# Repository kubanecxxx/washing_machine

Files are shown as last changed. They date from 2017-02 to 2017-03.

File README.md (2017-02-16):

# washing_machine
Old automatic washing machine electronic controller

This is and old washing machine renovation. The main reason for this project is the old mechanical programmer got cracked and the price for a new one was almost price of a new washing machine.

The project page is hosted on hackaday.io: https://hackaday.io/project/19873-washing-machine-renovation

Machine itself
----
Washing machine type is <b>Ardo A900</b>. It has basic features like:
- two speed motor with 5uF condenser
- water filling valve
- water drain pump
- water heater
- front door electric lock
- low and high level water level switch
- temperature switch
- few front panel switches (most of them are not used any more)

Hardware part
-----

Schematics and board layout are drawed in Eagle version 6. I used STM32F100C6 micronctroller.

The reason for using triacs instead of relays was switching in zero crossing of sine voltage. I used relays in previous version of this project and I had a lot of problems with this. Relay contacts got welded, switching caused microcontroller unhandled exceptions etc.

With triacs there are no more problems with MCU unhandled exceptions. But the water heater triac dissipates almost 10Watts of heat. It means <b>huge heatsink</b> is needed.

Software part
----

Software is based on ChibiOS real time operating system for microntollers. I made [CMake fork](https://github.com/kubanecxxx/chibios_fork) of the ChibiOS - it is my repositories. You probably need to clone this repository to build this project or you can take the data from the [CMakeLists.txt](fw/CMakeLists.txt) and create a ChibiOS Makefile or just edit the CMakeLists (you will probably need to adjust path to the GCC toolchain and path to the ChibiOS directory) to build this project on you machine.

Development toolchain is GNU arm gcc (https://launchpadlibrarian.net/209776202/gcc-arm-none-eabi-4_9-2015q2-20150609-linux.tar.bz2) version 4.9 - it contains interesting newlib library which saves a lot of RAM and hardware floating point support and many other features.

You can flash the MCU via openocd or my [kstlink](https://github.com/kubanecxxx/kstlink) project which is simple gdb server to debug and flash STM microcontrollers (I feel openocd too heavy).

Firmware is not well documented yet.

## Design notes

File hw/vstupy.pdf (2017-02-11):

List1

Stránka 1

vstupy
PA3 | door locked
PA4 | fuse zbytek ok
PA5 | fuse motor ok
PA6 | fuse heat ok
PB13 | low level | hladinoměr nízká úroven
PB14 | high level | hladinoměr vysoká úroven
PB15 | temperature termostat
PA8 | nezdimat | přepínač předvolba neždímat

výstupy
PA7 | lock | zamčít
PB0 | valve | napouštět
PB1 | pump | vypouštět
PB2 | M3 | motor rychle
PB10 | M2 | motor pomalu jeden směr
PB11 | M1 | motor pomalu druhý směr
PB12 | heat | topit

ovládání
PA0 | TIM2_CH1 | enkoder A
PA1 | TIM2_CH2 | enkoder B
PA2 | | enkoder switch
PB8 | I2C1_SCL | I2C display přemapovat I2C1
PB9 | I2C1_SDA | I2C display přemapovat I2C1

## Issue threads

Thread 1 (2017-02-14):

hardware update HW1.2

kubanecxxx, 2017-02-14:
Schematic and board should be updated.
----

- Heating triac is out of board right now -  there should be a connector for it
- there are a lot of neutral wires - dedicated connector with 3 or 4 wires just for neutral
- backup battery is much bigger than thought - holes for the battery holder (cable tie) should be elsewhere

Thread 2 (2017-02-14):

State machine status rememeber after powerdown

kubanecxxx, 2017-02-14:
Current state - automatic state machine is reset during powerup.

+ State machine should be memorised
+ After powerup the GUI should ask for continue or restart

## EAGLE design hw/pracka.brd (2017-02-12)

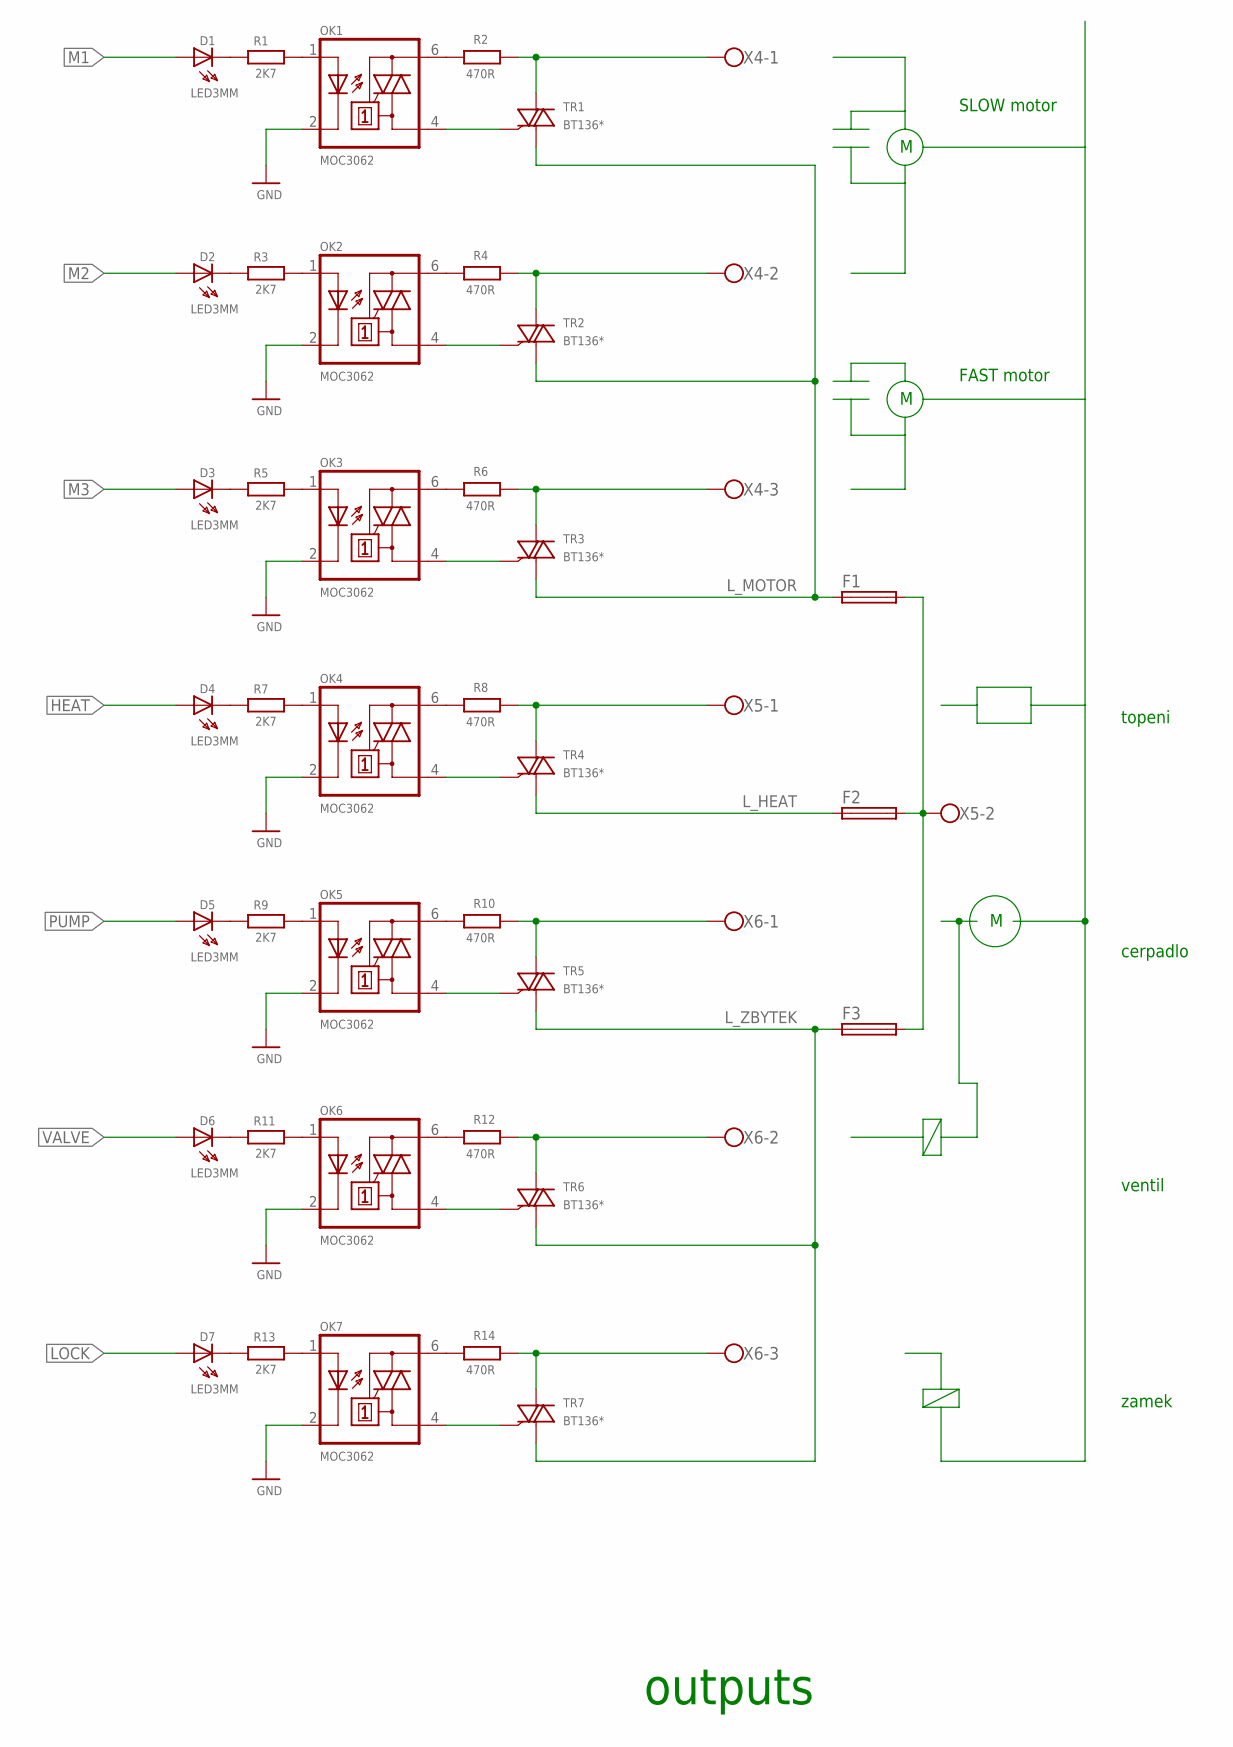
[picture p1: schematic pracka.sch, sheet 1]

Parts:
D1, D2, D3, D4, D5, D6, D7: LED3MM; LED3MM@1
F1, F2, F3: SH22,5A
OK1, OK2, OK3, OK4, OK5, OK6, OK7: MOC3062; DIL06
R1, R3, R5, R7, R9, R11, R13: 2K7; R0805
R2, R4, R6, R8, R10, R12, R14: 470R; 0207/7
TR1, TR2, TR3, TR4, TR5, TR6, TR7: BT136*; TO220DS
X4: W237-03P; W237-133
X5: W237-02P; W237-132
X6: W237-3E

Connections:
GND: OK1.2 (K), OK2.2 (K), OK3.2 (K), OK4.2 (K), OK5.2 (K), OK6.2 (K), OK7.2 (K); also elsewhere on the board
HEAT: D4.A; also elsewhere on the board
LOCK: D7.A; also elsewhere on the board
L_HEAT: F2.1, TR4.A1; also elsewhere on the board
L_MOTOR: F1.1, TR1.A1, TR2.A1, TR3.A1; also elsewhere on the board
L_ZBYTEK: F3.1, TR5.A1, TR6.A1, TR7.A1; also elsewhere on the board
M1: D1.A; also elsewhere on the board
M2: D2.A; also elsewhere on the board
M3: D3.A; also elsewhere on the board
unnamed: OK1.1 (A), R1.2
unnamed: OK2.1 (A), R3.2
unnamed: OK2.4 (A1), TR2.G
unnamed: D1.K (C), R1.1
unnamed: D2.K (C), R3.1
unnamed: OK1.4 (A1), TR1.G
unnamed: OK2.6 (A2), R4.1
unnamed: OK3.1 (A), R5.2
unnamed: OK3.4 (A1), TR3.G
unnamed: D3.K (C), R5.1
unnamed: OK3.6 (A2), R6.1
unnamed: OK4.1 (A), R7.2
unnamed: OK4.4 (A1), TR4.G
unnamed: D4.K (C), R7.1
unnamed: OK4.6 (A2), R8.1
unnamed: OK5.1 (A), R9.2
unnamed: OK5.4 (A1), TR5.G
unnamed: D5.K (C), R9.1
unnamed: OK5.6 (A2), R10.1
unnamed: OK6.1 (A), R11.2
unnamed: OK6.4 (A1), TR6.G
unnamed: D6.K (C), R11.1
unnamed: OK6.6 (A2), R12.1
unnamed: OK7.1 (A), R13.2
unnamed: OK7.4 (A1), TR7.G
unnamed: D7.K (C), R13.1
unnamed: OK7.6 (A2), R14.1
unnamed: F1.2, F2.2, F3.2, X5.2
unnamed: OK1.6 (A2), R2.1
PUMP: D5.A; also elsewhere on the board
P_HEAT: R8.2, TR4.A2, X5.1
P_LOCK: R14.2, TR7.A2, X6.3
P_M1: R2.2, TR1.A2, X4.1
P_M2: R4.2, TR2.A2, X4.2
P_M3: R6.2, TR3.A2, X4.3
P_PUMP: R10.2, TR5.A2, X6.1
P_VALVE: R12.2, TR6.A2, X6.2
VALVE: D6.A; also elsewhere on the board

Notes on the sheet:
topeni
cerpadlo
ventil
zamek
outputs
SLOW motor
FAST motor

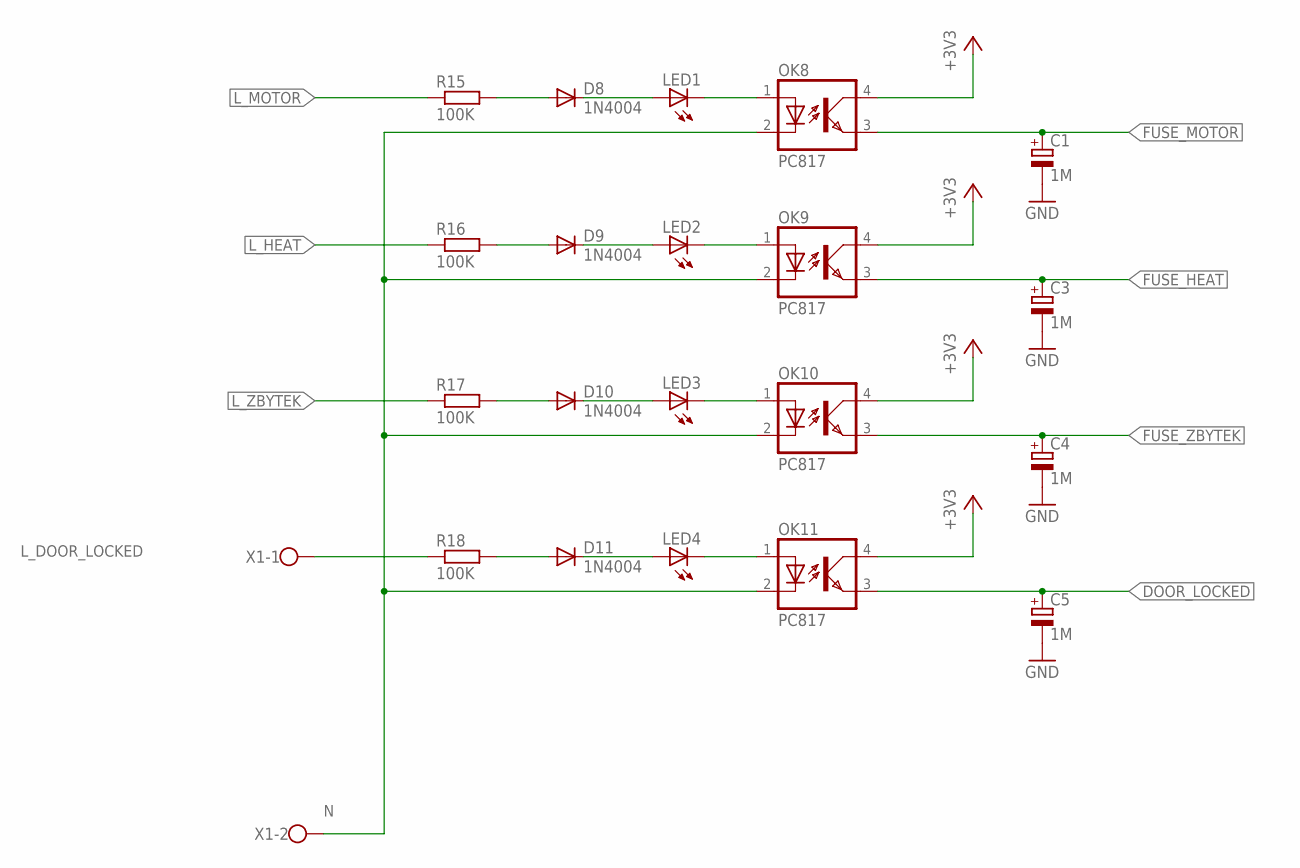
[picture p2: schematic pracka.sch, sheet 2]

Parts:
C1, C3, C4, C5: 1M; E2,5-5
D8, D9, D10, D11: 1N4004; DO41-10
LED1, LED2, LED3, LED4: LED3MM
OK8, OK9, OK10, OK11: PC817; DIL04
R15, R16, R17, R18: 100K; 0207/7
X1: W237-02P; W237-132

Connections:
+3V3: OK8.4 (COL), OK9.4 (COL), OK10.4 (COL), OK11.4 (COL); also elsewhere on the board
DOOR_LOCKED: C5.+, OK11.3 (EMIT); also elsewhere on the board
FUSE_HEAT: C3.+, OK9.3 (EMIT); also elsewhere on the board
FUSE_MOTOR: C1.+, OK8.3 (EMIT); also elsewhere on the board
FUSE_ZBYTEK: C4.+, OK10.3 (EMIT); also elsewhere on the board
GND: C1.-, C3.-, C4.-, C5.-; also elsewhere on the board
L_DOOR_LOCKED: R18.1, X1.1
L_HEAT: R16.1; also elsewhere on the board
L_MOTOR: R15.1; also elsewhere on the board
L_ZBYTEK: R17.1; also elsewhere on the board
N: OK8.2 (C), OK9.2 (C), OK10.2 (C), OK11.2 (C), X1.2
unnamed: D8.A, R15.2
unnamed: D8.C, LED1.A
unnamed: LED1.K (C), OK8.1 (A)
unnamed: D9.A, R16.2
unnamed: D9.C, LED2.A
unnamed: LED2.K (C), OK9.1 (A)
unnamed: D10.A, R17.2
unnamed: D10.C, LED3.A
unnamed: LED3.K (C), OK10.1 (A)
unnamed: D11.A, R18.2
unnamed: D11.C, LED4.A
unnamed: LED4.K (C), OK11.1 (A)

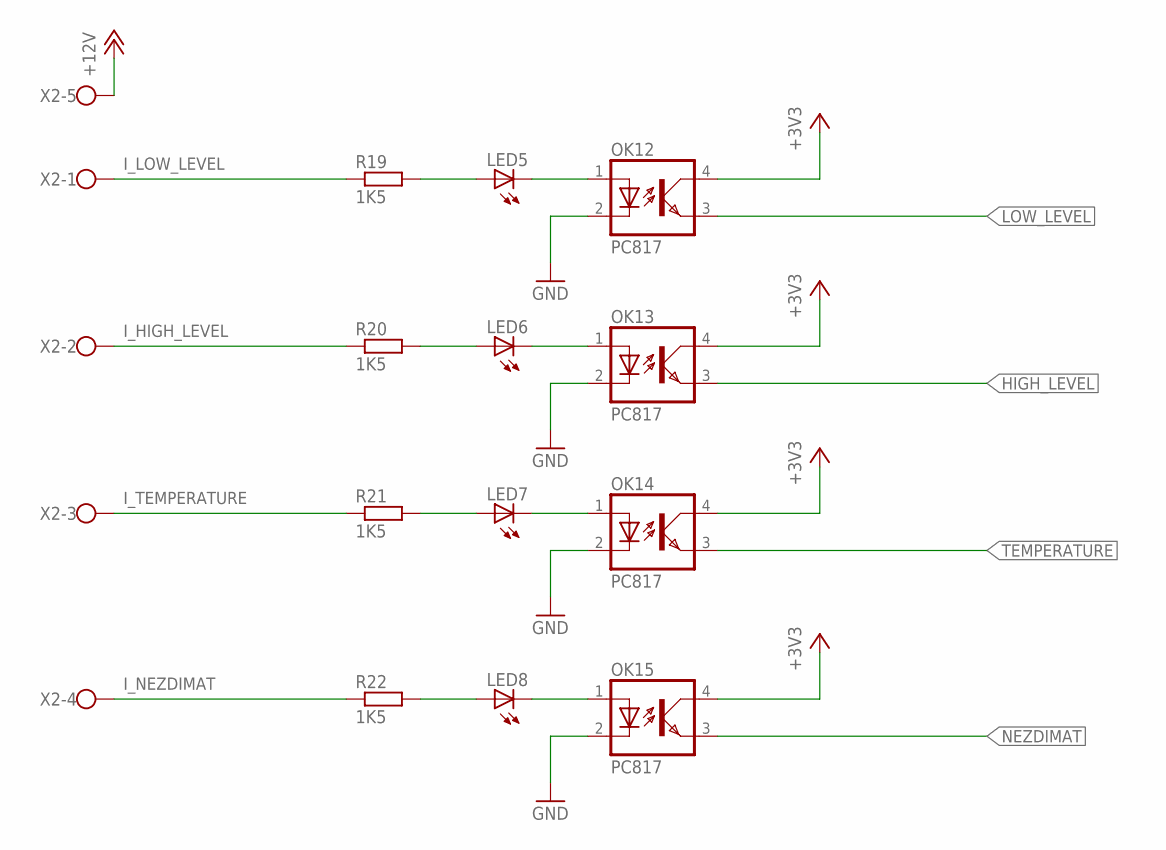
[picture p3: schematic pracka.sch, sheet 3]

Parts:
LED5, LED6, LED7, LED8: LED3MM
OK12, OK13, OK14, OK15: PC817; DIL04
R19, R20, R21, R22: 1K5; R0805
X2: W237-05P; W237-5P

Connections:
+3V3: OK12.4 (COL), OK13.4 (COL), OK14.4 (COL), OK15.4 (COL); also elsewhere on the board
+12V: X2.5; also elsewhere on the board
GND: OK12.2 (C), OK13.2 (C), OK14.2 (C), OK15.2 (C); also elsewhere on the board
HIGH_LEVEL: OK13.3 (EMIT); also elsewhere on the board
I_HIGH_LEVEL: R20.1, X2.2
I_LOW_LEVEL: R19.1, X2.1
I_NEZDIMAT: R22.1, X2.4
I_TEMPERATURE: R21.1, X2.3
LOW_LEVEL: OK12.3 (EMIT); also elsewhere on the board
unnamed: LED5.A, R19.2
unnamed: LED6.K (C), OK13.1 (A)
unnamed: LED5.K (C), OK12.1 (A)
unnamed: LED6.A, R20.2
unnamed: LED7.K (C), OK14.1 (A)
unnamed: LED7.A, R21.2
unnamed: LED8.K (C), OK15.1 (A)
unnamed: LED8.A, R22.2
NEZDIMAT: OK15.3 (EMIT); also elsewhere on the board
TEMPERATURE: OK14.3 (EMIT); also elsewhere on the board

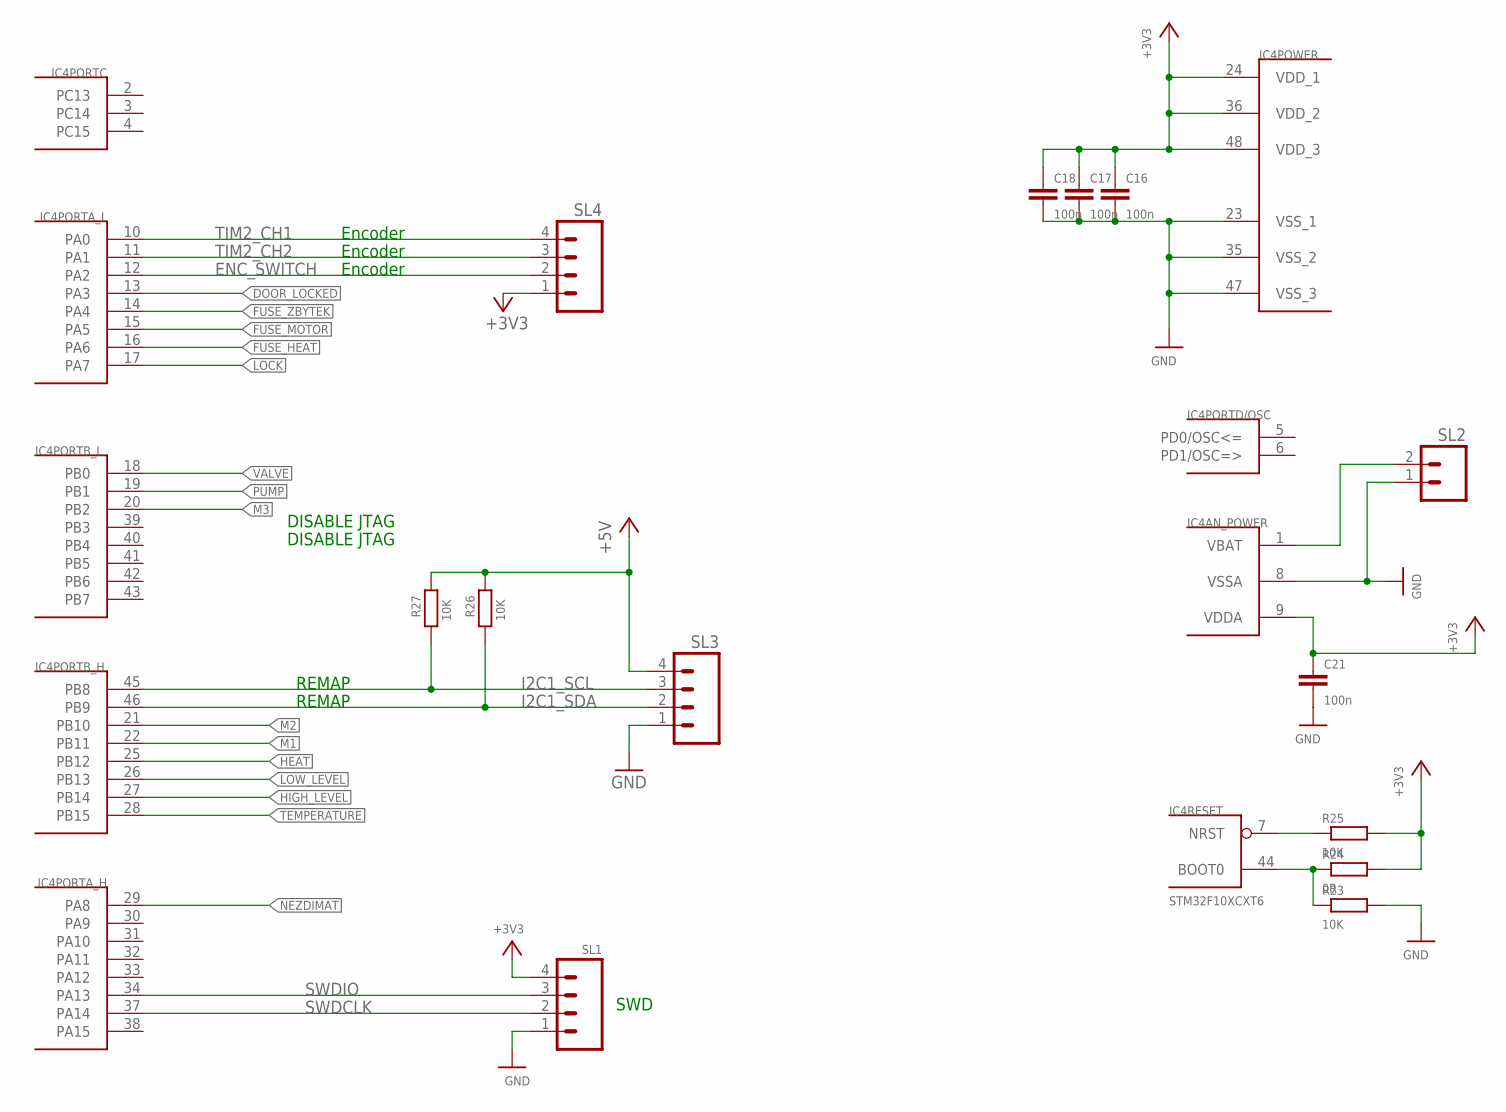
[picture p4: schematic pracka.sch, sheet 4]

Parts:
C16, C17, C18, C21: 100n; C1206
IC4: STM32F10XCXT6; TQFP48
R23, R25, R26, R27: 10K; R0805
R24: 0R; R0805
SL1, SL3, SL4: M04; 04P
SL2: M02; 02P

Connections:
+3V3: C16.1, C17.1, C18.1, C21.1, IC4.9 (VDDA), IC4.24 (VDD_1), IC4.36 (VDD_2), IC4.48 (VDD_3), R24.2, R25.2, SL1.4, SL4.1; also elsewhere on the board
+5V: R26.2, R27.2, SL3.4; also elsewhere on the board
DOOR_LOCKED: IC4.13 (PA3); also elsewhere on the board
ENC_SWITCH: IC4.12 (PA2), SL4.2
FUSE_HEAT: IC4.16 (PA6); also elsewhere on the board
FUSE_MOTOR: IC4.15 (PA5); also elsewhere on the board
FUSE_ZBYTEK: IC4.14 (PA4); also elsewhere on the board
GND: C16.2, C17.2, C18.2, C21.2, IC4.8 (VSSA), IC4.23 (VSS_1), IC4.35 (VSS_2), IC4.47 (VSS_3), R23.2, SL1.1, SL2.1, SL3.1; also elsewhere on the board
HEAT: IC4.25 (PB12); also elsewhere on the board
HIGH_LEVEL: IC4.27 (PB14); also elsewhere on the board
I2C1_SCL: IC4.45 (PB8), R27.1, SL3.3
I2C1_SDA: IC4.46 (PB9), R26.1, SL3.2
LOCK: IC4.17 (PA7); also elsewhere on the board
LOW_LEVEL: IC4.26 (PB13); also elsewhere on the board
M1: IC4.22 (PB11); also elsewhere on the board
M2: IC4.21 (PB10); also elsewhere on the board
M3: IC4.20 (PB2); also elsewhere on the board
unnamed: IC4.44 (BOOT0), R23.1, R24.1
unnamed: IC4.1 (VBAT), SL2.2
NEZDIMAT: IC4.29 (PA8); also elsewhere on the board
NRST: IC4.7 (NRST), R25.1
PUMP: IC4.19 (PB1); also elsewhere on the board
SWDCLK: IC4.37 (PA14), SL1.2
SWDIO: IC4.34 (PA13), SL1.3
TEMPERATURE: IC4.28 (PB15); also elsewhere on the board
TIM2_CH1: IC4.10 (PA0), SL4.4
TIM2_CH2: IC4.11 (PA1), SL4.3
VALVE: IC4.18 (PB0); also elsewhere on the board

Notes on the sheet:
SWD
REMAP
Encoder
DISABLE JTAG

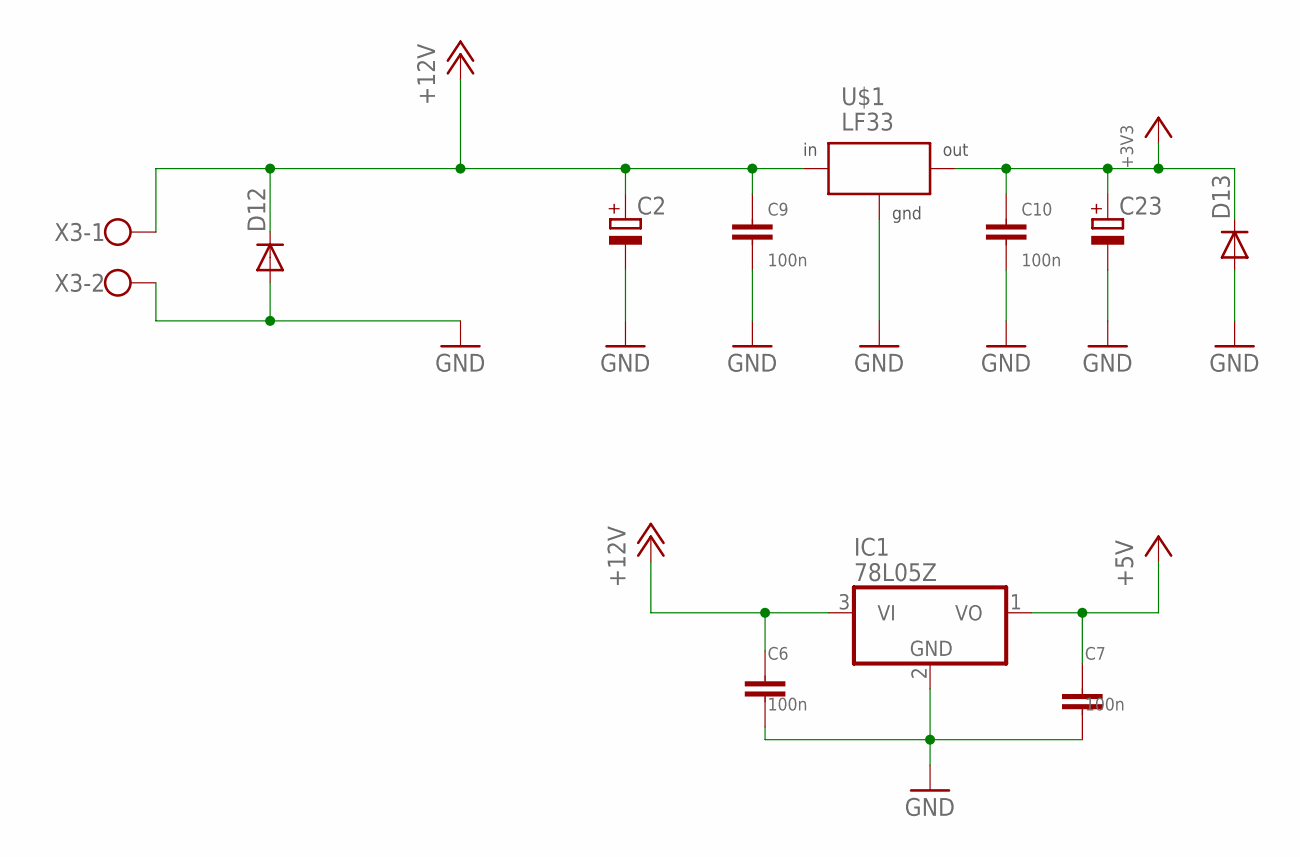
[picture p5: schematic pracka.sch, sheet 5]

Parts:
C2, C23: CPOL-EUE2.5-7; E2,5-7
C6, C7, C9, C10: 100n; C1206
D12, D13: DIODE-SMC; SMC
IC1: 78L05Z; TO92
U$1: LF33; DPACK
X3: W237-02P; W237-132

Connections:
+3V3: C10.1, C23.+, D13.C, U$1.3 (OUT); also elsewhere on the board
+5V: C7.1, IC1.1 (VO); also elsewhere on the board
+12V: C2.+, C6.1, C9.1, D12.C, IC1.3 (VI), U$1.1 (IN), X3.1; also elsewhere on the board
GND: C2.-, C6.2, C7.2, C9.2, C10.2, C23.-, D12.A, D13.A, IC1.2 (GND), U$1.2 (GND), X3.2; also elsewhere on the board

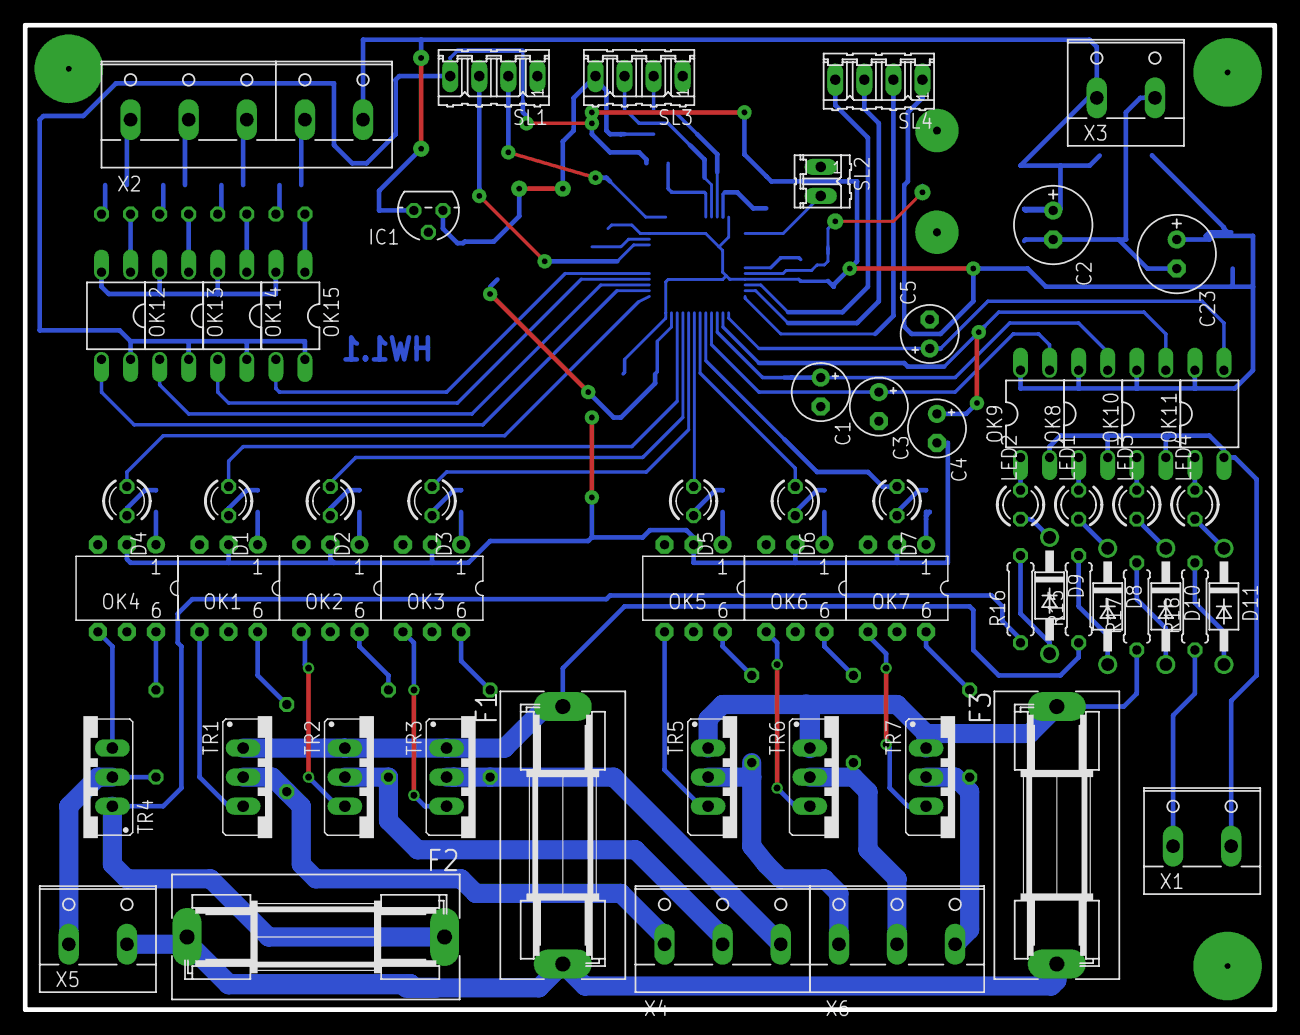
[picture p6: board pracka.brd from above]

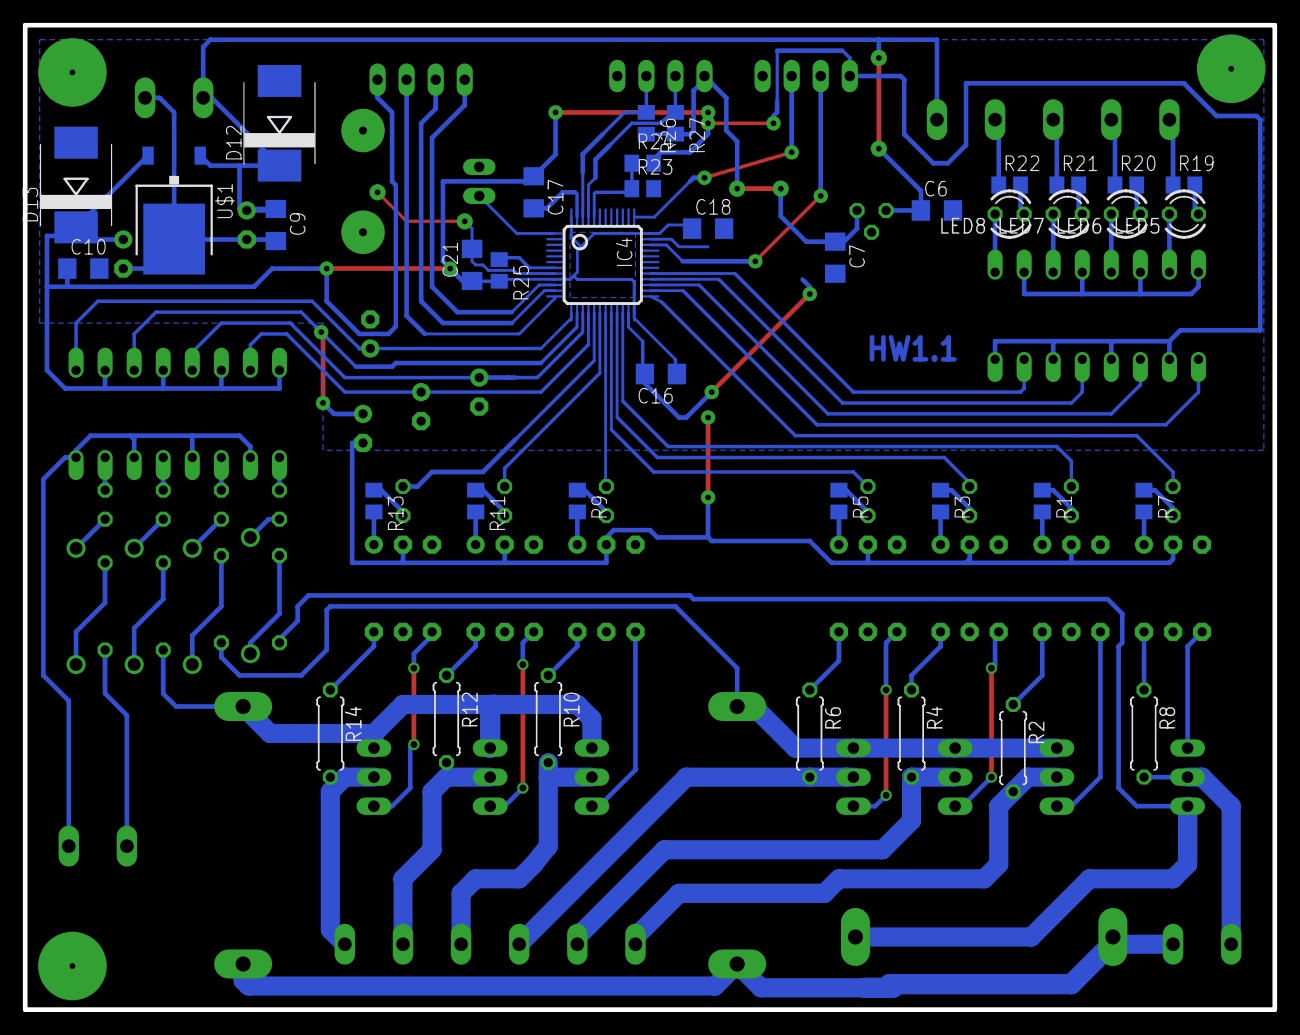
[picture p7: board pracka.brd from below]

Board: 2 copper layers, 109.2 x 86.0 mm, 100 parts (39 on the bottom side), 94 nets.

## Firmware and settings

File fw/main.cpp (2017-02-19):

/*
 ChibiOS/RT - Copyright (C) 2006-2013 Giovanni Di Sirio

 Licensed under the Apache License, Version 2.0 (the "License");
 you may not use this file except in compliance with the License.
 You may obtain a copy of the License at

 http://www.apache.org/licenses/LICENSE-2.0

 Unless required by applicable law or agreed to in writing, software
 distributed under the License is distributed on an "AS IS" BASIS,
 WITHOUT WARRANTIES OR CONDITIONS OF ANY KIND, either express or implied.
 See the License for the specific language governing permissions and
 limitations under the License.
 */

#include "ch.h"
#include "hal.h"
//#include "scheduler.hpp"
#include "relays.h"
#include "LCD_ctrl.h"
#include "rotary_encoder.h"
#include "scheduler.h"
#include "inputs.h"
#include "gui.h"
#include "statemachine.h"

systime_t sysTime;

/*
 * Application entry point.
 */

void mcu_init(void);

uint8_t changed = 0;
char lcd_data[100];


void lcd_task(void)
{
    if (changed)
    {
        changed = 0;

        LCD_xy(0,0);
        LCD_puts(lcd_data);
    }
}

static delay_t dt;
void blik(void * a);
void test(void);

static THD_WORKING_AREA(gui_wa, 512);

Gui _gui;


void gui_thread(void *)
{
    LCD_xy(0,0);
    LCD_puts("Dobry den");
    chThdSleepSeconds(2);    
    while(TRUE)
    {
        rotenc_task();
        _gui.task();
    }
}


void enable_watchdog(void)
{
    //setup watchdog
    DBGMCU->CR |= DBGMCU_CR_DBG_IWDG_STOP;
    IWDG->KR = 0x5555;
    IWDG->PR = 6;
    IWDG->RLR = 0xFFF;
    IWDG->KR = 0xCCCC;
}



void clear_watchdog(void)
{
    IWDG->KR = 0xAAAA;
}

int main(void)
{
    halInit();
    chSysInit();

    mcu_init();
    enable_watchdog();

    //test();

    RCC->APB1ENR |= RCC_APB1ENR_PWREN | RCC_APB1ENR_BKPEN;
    PWR->CR |= PWR_CR_DBP;

    statemachine _state_machine(params, _gui);


    shFillStruct(&dt, blik, NULL, MS2ST(500), PERIODIC);
    shRegisterStruct(&dt);


    //inform user the watchdog event occured
    if (RCC->CSR & (RCC_CSR_IWDGRSTF | RCC_CSR_WWDGRSTF
                   ))
        _gui.change_menu(8);
    else
        RCC->CSR |= RCC_CSR_RMVF;

    chThdCreateStatic(&gui_wa,sizeof(gui_wa), LOWPRIO, gui_thread, NULL);

	while (TRUE)
	{        
        chThdSleepMilliseconds(5);
        inputs_read();

        //if (chVTGetSystemTime() < S2ST(10))
        clear_watchdog();
        _state_machine.task();
        sysTime = chVTGetSystemTime();
        shPlay();
        relay_writeall();

        //lcd_task();
	}

	return 1;
}

void mcu_init(void)
{
    relay_init();
    outputs.status = 0;
    relay_writeall();

    inputs_init();
    rotenc_init();



    LCD_init();
    LCD_init();


}

void blik(void * a)
{
    return;
    if (!_gui.atMainScreen())
        outputs_forced.u.motor_fast ^= 1;
}

void test(void)
{

    while(TRUE)
    {
        for (unsigned char i = 0; i < 8; i++)
        {
            LCD_clear();
            uint8_t a = i;
            LCD_xy(a,0);
            LCD_puts("Hi!");
            chThdSleepMilliseconds(500);
        }
        for (uint8_t i = 8 ; i > 0 ; i--)
        {
            LCD_clear();
            uint8_t a = i;
            LCD_xy(a,0);
            LCD_puts("Hi!");
            chThdSleepMilliseconds(500);
        }
    }

    while (TRUE)
    {
        inputs_read();
        outputs.u.doorlock = inputs.b.fuse_heat;
        outputs.u.heater = inputs.b.fuse_motor;
        outputs.u.motor_fast = inputs.b.fuse_zbytek;
        outputs.u.valve = inputs.b.door;
        relay_writeall();
    }

    while (TRUE)
    {
        for ( uint8_t i = 0; i < RELAY_COUNT; i++)
        {
            outputs.status = 1 << i;
            relay_writeall();

            chThdSleepMilliseconds(500);
        }
    }
}

#ifdef __cplusplus

extern "C" void __cxa_pure_virtual(void)
{
    asm("bkpt");
    while(1);
}

#endif

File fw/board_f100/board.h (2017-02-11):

/*
    ChibiOS/RT - Copyright (C) 2006,2007,2008,2009,2010,
                 2011,2012 Giovanni Di Sirio.

    This file is part of ChibiOS/RT.

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
    You should have received a copy of the GNU General Public License
    along with this program.  If not, see <http://www.gnu.org/licenses/>.
*/

#ifndef _BOARD_H_
#define _BOARD_H_

/*
 * Setup for STMicroelectronics STM32VL-Discovery board.
 */

/*
 * Board identifier.
 */
//#define BOARD_ST_STM32VL_DISCOVERY
#define BOARD_NAME              "ST washing machine"

/*
 * Board frequencies.
 */
#define STM32_LSECLK            32768
#define STM32_HSECLK            4000000

/*
 * MCU type, supported types are defined in ./os/hal/platforms/hal_lld.h.
 */
#define STM32F10X_MD_VL

/*
 * IO pins assignments.
 */
#define GPIOA_BUTTON            0
#define GPIOA_SPI1NSS           4

#define GPIOB_SPI2NSS           12

#define GPIOC_LED4              8
#define GPIOC_LED3              9

/*
 * I/O ports initial setup, this configuration is established soon after reset
 * in the initialization code.
 *
 * The digits have the following meaning:
 *   0 - Analog input.
 *   1 - Push Pull output 10MHz.
 *   2 - Push Pull output 2MHz.
 *   3 - Push Pull output 50MHz.
 *   4 - Digital input.
 *   5 - Open Drain output 10MHz.
 *   6 - Open Drain output 2MHz.
 *   7 - Open Drain output 50MHz.
 *   8 - Digital input with PullUp or PullDown resistor depending on ODR.
 *   9 - Alternate Push Pull output 10MHz.
 *   A - Alternate Push Pull output 2MHz.
 *   B - Alternate Push Pull output 50MHz.
 *   C - Reserved.
 *   D - Alternate Open Drain output 10MHz.
 *   E - Alternate Open Drain output 2MHz.
 *   F - Alternate Open Drain output 50MHz.
 * Please refer to the STM32 Reference Manual for details.
 */

/*
 * Port A setup.
 * Everything input with pull-up except:
 * PA0  - Normal input      (BUTTON).
 * PA2  - Alternate output  (USART2 TX).
 * PA3  - Normal input      (USART2 RX).
 * PA4  - Push pull output  (SPI1 NSS), initially high state.
 * PA5  - Alternate output  (SPI1 SCK).
 * PA6  - Normal input      (SPI1 MISO).
 * PA7  - Alternate output  (SPI1 MOSI).
 * PA9  - Alternate output  (USART1 TX).
 * PA10 - Normal input      (USART1 RX).
 */
#define VAL_GPIOACRL            0x44B33333      /*  PA7...PA0 */
#define VAL_GPIOACRH            0x888884B8      /* PA15...PA8 */
#define VAL_GPIOAODR            0xFFFFfFFF

/*
 * Port B setup.
 * Everything input with pull-up except:
 * PB12 - Push pull output  (SPI2 NSS), initially high state.
 * PB13 - Alternate output  (SPI2 SCK).
 * PB14 - Normal input      (SPI2 MISO).
 * PB15 - Alternate output  (SPI2 MOSI).
 */
#define VAL_GPIOBCRL            0x88888444      /*  PB7...PB0 */
#define VAL_GPIOBCRH            0xB4B44488      /* PB15...PB8 */
#define VAL_GPIOBODR            0xFFFFFFFF

/*
 * Port C setup.
 * Everything input with pull-up except:
 * PC8  - Push-pull output (LED4), initially low state.
 * PC9  - Push-pull output (LED3), initially low state.
 */
#define VAL_GPIOCCRL            0x88888888      /*  PC7...PC0 */
#define VAL_GPIOCCRH            0x88888833      /* PC15...PC8 */
#define VAL_GPIOCODR            0xFFFFFCFF

/*
 * Port D setup.
 * Everything input with pull-up except:
 * PD0  - Normal input (XTAL).
 * PD1  - Normal input (XTAL).
 */
#define VAL_GPIODCRL            0x88888844      /*  PD7...PD0 */
#define VAL_GPIODCRH            0x88888888      /* PD15...PD8 */
#define VAL_GPIODODR            0xFFFFFFFF

/*
 * Port E setup.
 * Everything input with pull-up except:
 */
#define VAL_GPIOECRL            0x88888888      /*  PE7...PE0 */
#define VAL_GPIOECRH            0x88888888      /* PE15...PE8 */
#define VAL_GPIOEODR            0xFFFFFFFF

#if !defined(_FROM_ASM_)
#ifdef __cplusplus
extern "C" {
#endif
  void boardInit(void);
#ifdef __cplusplus
}
#endif
#endif /* _FROM_ASM_ */

#endif /* _BOARD_H_ */

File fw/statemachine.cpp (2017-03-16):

#include "statemachine.h"
#include "inputs.h"
#include "relays.h"
#include "chsprintf.h"
#include <string.h>

statemachine * statemachine::_instance = NULL;

ton::ton()
{
    old_systime = chVTGetSystemTime();
    edge = false;    
}

bool ton::task(bool en, uint32_t systime, uint32_t * remains)
{
    uint32_t s = chVTGetSystemTime();
    if (en && !edge)
    {
        old_systime = s;
    }
    edge = en;

    int32_t r = old_systime + systime - s;
    if (r < 0)
        r = 0;
    _remains = r;

    if (remains)
    {        
        *remains = r;
    }
    if (en)
    {
        if (s - old_systime > systime)
        {
            return true;
        }
    }

    return false;
}

void ton::format_remains(char * buffer)
{
    uint32_t s = ST2S(_remains);

    chsprintf(buffer, "%02d:%02d", s / 60, s %60);
}

statemachine::statemachine(const parameters_t & pars, const Gui & gui):
    _state((*((state_t*)(&(BKP->DR1))))),
    _rinsing(_DR(5)),
    _forced(_DR(6)),
    _gui(gui),
    _pars(pars)
{
    _instance = this;

    //_state = REFILL;
    //_forced = false;
    //_rinsing = 0;


    _state = START;

    alarms.word = 0;

    /*
    _pair[0].state = WASH_TIME;
    _pair[0].timer = &_T_wash;

    _pair[1].state = SPIN_TIME;
    _pair[1].timer = &_T_spin;

    _pair[2].state = RINSE_TIME;
    _pair[2].timer = &_T_rinse;

    _pair[3].state = FINAL_SPIN;
    _pair[3].timer = &_T_last_spin;
    */

    //setup the right timer after powerdown
}

void statemachine::task()
{
    bool main = _gui.atMainScreen();
    bool spin_screen = _gui.atSpinScreen();

    //timers
    bool t_start = _T_start.task(inputs.b.enc_switch && inputs.b.door, MS2ST(1000));
    bool t_prani = _T_wash.task(_state == WASH_TIME, S2ST(_pars.doba_prani * NASOBITKO));
    bool t_empty = _T_empty.task(_state == WATER_OUT && !inputs.b.low_level, S2ST(30));
    bool t_spin = _T_spin.task(_state == SPIN_TIME, S2ST(_pars.doba_zdimani * NASOBITKO));
    bool t_rinse = _T_rinse.task(_state == RINSE_TIME, S2ST(_pars.doba_machani) * NASOBITKO);
    bool t_empty2 = _T_empty2.task(_state == FINAL_WATER_OUT && !inputs.b.low_level, S2ST(30));
    bool t_last_spin = _T_last_spin.task(_state == FINAL_SPIN, S2ST(NASOBITKO*_pars.posledni_zdimani));

    if (_state == START && main && t_start)
    {
        _state = WATER;
        _rinsing = 0;
        _forced = false;
    }

    if (_state == START && spin_screen && t_start)
    {
        _state = FINAL_SPIN;
        _rinsing = 0;
        _forced = false;
    }

    else if (_state == WATER && inputs.b.high_level)
    {
        _state = HEAT;
    }

    else if (_state == HEAT && inputs.b.temperature)
    {
        _state = WASH_TIME;        
    }

    else if (t_prani)
    {
        _state = WATER_OUT;
    }

    else if ( t_empty)
    {
        _state = SPIN_TIME;
    }

    else if (t_spin)
    {
        _state = REFILL;
    }

    else if (_state == REFILL && inputs.b.high_level)
    {
        _state = RINSE_TIME;
    }

    else if (t_rinse)
    {
        if (++_rinsing >= _pars.pocet_machani)
        {
            _state = FINAL_WATER_OUT;
        }
        else
        {
            _state = WATER_OUT;
        }
    }

    else if (t_empty2)
    {
        if (inputs.b.nezdimat || _forced)
        {
            _state = START;
        }
        else
        {
            _state = FINAL_SPIN;
        }
    }

    else if(t_last_spin)
    {
        _state = START;
    }

    if (_T_reset.task(_state != START && inputs.b.enc_switch, S2ST(10)))
    {
        _state = FINAL_WATER_OUT;
        _forced = true;
    }

    if (_T_reset2.task(inputs.b.enc_switch, S2ST(15)))
    {
        reset();
    }

    //valve during spin simple sequencer
    bool spin = _state == FINAL_SPIN || _state == SPIN_TIME;
    _final_spin_pump_sub_machine =
            _T_final_spin_pump.task(spin && !_fspsm2 , S2ST(10));
    _fspsm2 = _T_final_spin_pump2.task(spin && _final_spin_pump_sub_machine, S2ST(15));
    bool pump = spin && !_final_spin_pump_sub_machine;

    outputs.u.heater = ((_state == WASH_TIME || _state == HEAT || _state == WATER)
                        && !inputs.b.temperature && inputs.b.low_level && inputs.b.door);
    outputs.u.valve = ((_state == WATER || _state == REFILL) && !inputs.b.high_level && inputs.b.door);
    outputs.u.pump = (_state == WATER_OUT || _state == FINAL_WATER_OUT || pump);
    outputs.u.doorlock = _state != START;

    //substate machine - washing there and back
    if ((_state == WASH_TIME || _state == RINSE_TIME) && inputs.b.door)
    {
        _slow.task(LOW_SPEED);
    }
    else if ((_state == SPIN_TIME || _state == FINAL_SPIN) && inputs.b.door)
    {
        speed_t s = HIGH_SPEED;

        if (_pars.otacky_zdimani == 0)
            s = LOW_SPEED;

        if (s == LOW_SPEED)
            _slow.task(s,120,10);
        else
            _slow.slow_startup();
    }
    else if (_state == HEAT || (_state == WATER && outputs.u.heater ))
    {
        _slow.task(LOW_SPEED, 2, 10);
    }
    else
    {
        relay_stop_motor();
        _slow.reset();
    }

    alarm_processing();

    if (alarms.word)
    {
        outputs.u.heater = 0;
        outputs.u.valve = 0;
        outputs.u.pump = 0;
        relay_stop_motor();
    }
}

void statemachine::reset()
{
    _state = START;
    _forced = false;
    _rinsing = 0;

}

void statemachine::alarm_processing()
{
    alarms.names.ohrev_dlouho = _T_alarm_heat.task(_state == HEAT, S2ST(2700));
    alarms.names.napousteni_dlouho = _T_alarm_fill.task(_state == WATER || _state == REFILL, S2ST(180));

    alarms.names.porucha_hladinomeru = (!inputs.b.low_level && inputs.b.high_level);

    alarms.names.vypousteni_dlouho = _T_alarm_empting.task(
                _state == WATER_OUT || _state == FINAL_WATER_OUT, S2ST(180));


    alarms.names.dvere = !inputs.b.door && _state != START;

    alarms.names.fh = !inputs.b.fuse_heat;
    alarms.names.fm = !inputs.b.fuse_motor;
    alarms.names.fz = !inputs.b.fuse_zbytek;

}

void seq::task(speed_t speed, uint16_t rotate_time, uint16_t sleep_time)
{
    if (_tleft.task(_state == 0, S2ST(rotate_time)))
    {
        _state = 1;
    }
    else if (_toff.task(_state == 1, S2ST(sleep_time)))
    {
        _state = 2;
    }
    else if (_tright.task(_state == 2, S2ST(rotate_time)))
    {
        _state = 3;
    }
    else if (_toff2.task(_state == 3, S2ST(sleep_time)))
    {
        _state = 0;
    }

    if (_state == 0)
    {
        relay_start_motor(LEFT, speed);
    }
    else if (_state == 1)
    {
        relay_stop_motor();
    }
    else if (_state == 2)
    {
        relay_start_motor(RIGHT, speed);
    }
    else if (_state == 3)
    {
        relay_stop_motor();
    }
}
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

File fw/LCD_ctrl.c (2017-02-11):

#include "ch.h"
#include "hal.h"

#include "LCD_ctrl.h"
#include "display.h"

//global variables
static char string[5];

#ifdef LCD_PARALEL
#define LCD_SET(LCD_BIT) bit_set(LCD_control_port,LCD_BIT)
#define LCD_CLR(LCD_BIT) bit_clr(LCD_control_port,LCD_BIT)

// LCD port defitions
#define LCD_PORT 		PORTA
#define LCD_DDR			DDRA

// LCD signals definitions
#define LCD_RS 	3
#define LCD_E	0
#define LCD_RW	1

// LCD control macros
#define LCD_control_port PORTB
#define LCD_control_ddr	DDRB

#else
static I2CDriver * i2c;
static uint8_t port;

#define LCD_RS 	0
#define LCD_E	2
#define LCD_RW	1
#define LCD_D4  4
#define LCD_D5  5
#define LCD_D6  6
#define LCD_D7  7
#define LCD_BACKLIGHT 3

inline static void refresh_port(void)
{
    i2cMasterTransmit(i2c,PCF_ADDRESS, &port, 1, NULL,0);
}

inline static void LCD_CLR(uint8_t bitnum)
{
    port &= ~(1 << bitnum);
    //refresh_port();
}


inline static void LCD_SET(uint8_t bitnum)
{
    port |= 1 << bitnum;
    //refresh_port();
}

#endif

// LCD initialisation procedure
void LCD_init(void)
{	


#ifdef LCD_PARALEL
	LCD_DDR |= 0b00001111;
	LCD_control_ddr |= 0b00001011;
	LCD_CLR(LCD_RS);
	LCD_SET(LCD_E);
    LCD_PORT = (LCD_PORT &0xF0) | 0x04; //cursor home
	LCD_CLR(LCD_E);
	_delay_ms(10);
	LCD_SET(LCD_E);
	LCD_CLR(LCD_E);
	_delay_us(200);
	LCD_SET(LCD_E);
	LCD_CLR(LCD_E);
	_delay_us(60);
#else

    //init i2c driver under
    if (!i2c)
        i2c = display_init();
    port = 0;

    LCD_SET(LCD_BACKLIGHT);
    refresh_port();
    chThdSleepMilliseconds(100);
    refresh_port();
    chThdSleepMilliseconds(100);


    LCD_CLR(LCD_RS);
    refresh_port();
    LCD_SET(LCD_E);
    refresh_port();
    port |= 0x4 << 4; //cursor home
    refresh_port();
    LCD_CLR(LCD_E);
    refresh_port();


/*
    LCD_SET(LCD_E);
    refresh_port();
    LCD_CLR(LCD_E);
    refresh_port();
*/

#endif

	LCD_wr_cmd(0x20);  //4bits, line display, 5x7 dots
	LCD_wr_cmd(0x28);  //2 lines display
	LCD_clear();		
	LCD_wr_cmd(0x08);  //display off , cursor off , blinking off 	
	LCD_wr_cmd(0x0C);  //display on
	LCD_wr_cmd(0x06);  //increment , not shifted

    LCD_xy(0,0);
    LCD_puts("beda");

    asm("nop");

}


//convert input data to bargraph and print it
void LCD_bargraph(unsigned char data){
	unsigned char i,temp;

//	data/=4;
//	LCD_cgram_load_VU();

	i=data;
	i/=5;
	while(i--)
		LCD_wr_data(5);

	temp=i;
	i=data;
	i=i%5;

	LCD_wr_data(i);

	temp=13-temp;
	while(temp--)
		LCD_wr_data(0);

}

// write string to LCD
void LCD_puts (const char *c){
	unsigned char x;

	x=*c;
	while (x!=0) {
		LCD_wr_data(*c++);
		x=*c;
	}
}

// write program memory string to LCD - save RAM (more than brutally)
void LCD_putsflash (const char *c){	
	LCD_puttitle(c,0);
}

void LCD_puttitle(const char *c,unsigned char upper){
	unsigned char i; 
	char  temp[17];

	strcpy_P(temp,c);

	if (upper) strupr(temp);

	for(i=0;temp[i]!=0;i++)
		LCD_wr_data(temp[i]);
	
}

unsigned char LCD_bit_reverse (unsigned char data){
	unsigned char temp=0;
	temp+=(data>>3);
	temp+=((data>>2)&1)<<1;
	temp+=((data>>1)&1)<<2;
	temp+=(data & 1) << 3;
	
	return (temp&0x0f);	
}

// send command to LCD
void LCD_wr_cmd (unsigned char cmd)
{
#ifdef LCD_PARALEL
    unsigned char temp;
	temp=LCD_bit_reverse(cmd>>4);
	LCD_CLR(LCD_RS);
	LCD_SET(LCD_E);
	LCD_PORT = (LCD_PORT & 0xF0) | temp;
	LCD_CLR(LCD_E);
	LCD_SET(LCD_E);

	temp=LCD_bit_reverse(cmd&0x0f);
	LCD_PORT = (LCD_PORT & 0xF0) | temp;
	LCD_CLR(LCD_E);
	_delay_us(60);
	_delay_ms(2);
#else
    LCD_CLR(LCD_RS);
    LCD_SET(LCD_E);
    refresh_port();
    //LCD_PORT = (LCD_PORT & 0xF0) | temp;
    port &= 0b00001111;
    port |= cmd & 0xf0;
    refresh_port();
    LCD_CLR(LCD_E);
    refresh_port();
    LCD_SET(LCD_E);
    refresh_port();

    //LCD_PORT = (LCD_PORT & 0xF0) | temp;
    port &= 0b00001111;
    port |= (cmd &0xf) << 4;
    refresh_port();
    LCD_CLR(LCD_E);
    refresh_port();
    chThdSleepMilliseconds(1);
#endif
}

// send data to LCD
void LCD_wr_data (int data)
{
#ifdef LCD_PARALEL
	LCD_SET(LCD_E);
	LCD_SET(LCD_RS);
	LCD_PORT = (LCD_PORT & 0xF0) | (LCD_bit_reverse(data >> 4));
	LCD_CLR(LCD_E);
	LCD_SET(LCD_E);
	LCD_PORT = (LCD_PORT & 0xF0) | (LCD_bit_reverse(data & 0x0F));
	LCD_CLR(LCD_E);
	_delay_us(60);
#else
    LCD_SET(LCD_E);
    LCD_SET(LCD_RS);
    refresh_port();

    port &= 0b00001111;
    port |= data & 0xf0;
    refresh_port();
    LCD_CLR(LCD_E);
    refresh_port();

    LCD_SET(LCD_E);
    refresh_port();
    port &= 0b00001111;
    port |= (data &0xf) << 4;
    refresh_port();
    LCD_CLR(LCD_E);
    refresh_port();
    chThdSleepMilliseconds(1);
#endif

}


// set X,Y cursor position
void LCD_xy(unsigned char x,unsigned char y)
{
	unsigned char adr;
	y=y<<6;
	adr=x+y;
	adr+=0b10000000; 	//DD RAM address
	LCD_wr_cmd(adr);
}

char * uchar2string(char data_in, unsigned char sign_in){
	char temp;
	char sign;

	if(data_in==0) {
		strcpy(string,"   0");	
		return string;
	}
	
	if(data_in>0){
		if (sign_in) sign='+'; else sign=' ';
	} else {
		sign='-';
		data_in=-data_in;
	}

	*(string)=' ';
	temp=data_in/100;	
	data_in-=100*temp;
	if(!temp) temp=' '-48;
	*(string+1)=temp+48;

	temp=data_in/10;	
	data_in-=10*temp;
	if(!temp && (*(string+1)==' ')) temp=' '-48;
	*(string+2)=temp+48;

	*(string+3)=data_in+48;
	*(string+4)=0;

	if(string[2]==' '){
		string[2]=sign;
		return string;
	}

	if(string[1]==' '){
		string[1]=sign;
		return string;
	}
	string[0]=sign;
	return string;
}

void LCD_putnum(char data_in,unsigned char sign){
	LCD_puts(uchar2string(data_in,sign));
}

void LCD_putnum_left(char data_in,unsigned char sign){
	unsigned char i=0;

	uchar2string(data_in,sign);
	while (string[i] == ' ')
		i++;

	LCD_puts(i+string);
}

void LCD_putunsigned(unsigned char data){
	unsigned char temp;

	temp=data/100;	
	data-=100*temp;
	*(string)=temp+48;

	temp=data/10;	
	data-=10*temp;
	*(string+1)=temp+48;

	*(string+2)=data+48;
	*(string+3)=0;

	LCD_puts(string);
}


unsigned char LCD_log(unsigned char data_in){
	unsigned char temp;

	if (data_in <7){
		temp=3*data_in;
	} else
	if (data_in < 21){
		temp=data_in + 12;
	}
	if (data_in > 20){
		temp=data_in/5 + 28;
	}

	return (temp);
}

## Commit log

2017-02-12 small statemachine fixes, added display message - number of rinsing and spinning
    [gui.cpp, inputs.c, main.cpp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]
2017-02-12 hardware fixes
    [pracka.brd, pracka.sch]
2017-02-14 added watchdog to main file
    some time constants changed it the statemachine
    added feature to gui - current counter / counter preset
2017-02-18 Fixes #4
    Added startup screen when watchdog fails
    [gui.cpp, main.cpp]
2017-02-19 Fixes #4 - now really
    [gui.cpp, main.cpp]
2017-03-16 added new function - only spinning state machine switch from slow to high speed because of motor is too weak
    [gui.cpp, statemachine.cpp]
